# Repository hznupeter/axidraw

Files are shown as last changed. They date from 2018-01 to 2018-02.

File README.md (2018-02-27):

# axidraw 画图机器人
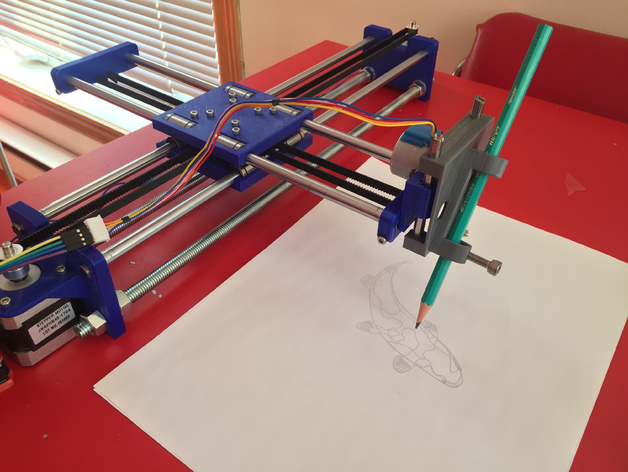
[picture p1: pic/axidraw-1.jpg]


## 3D打印件
打印3d_file 目录下的全部模型，其中x_motor_mount.stl需要打印2份。
模型文件来源https://www.thingiverse.com/thing:1514145

## 硬件
- arduino UNO 1块
- CNC shield v3雕刻机扩展板 1片
- A4988驱动芯片(带散热片) 3片
- 12V 3A监控电源 1个
- 28BYJ-48 5V 步进电机 1个
- 42步进电机 2个
- 短接帽 10个
- M3 8mm 螺丝 2个
- M3 20mm 螺丝10个
- M3 30mm 螺丝8个
- M3螺帽 22个
- M10螺帽 8个
- 直线光轴8mm*400mm 2根
- 直线光轴8mm*300mm 2根
- 直线光轴6mm*100mm 2根
- LM6UU直线轴承 2个
- LM8UU直线轴承 8个
- 2GT-16齿同步轮 内孔5mm 含顶丝 2个
- 16齿同步轮 被动轮 内孔3mm 1个
- 16齿 无齿轮 被动轮 内孔3mm 4个
- 2GT同步带 带宽6mm 2米

## 软件

- [Arduino IDE](https://www.arduino.cc/en/Main/Software)

给arduino UNO烧写固件。

- [grbl库](https://github.com/grbl/grbl)

用于给arduino UNO烧写该库。

- [Inkscape](https://inkscape.org/en/)

一个跨平台的开源软件，利用它的扩展功能可以生成G-code。

- [CNCjs](https://github.com/cncjs/cncjs/releases/latest)

一款CNC控制软件，支持中文，可以方便地将G-code传入到arduino UNO并执行程序。当然也可以使用其他符合grbl规范的软件，如[bCNC](https://github.com/vlachoudis/bCNC),[EleksCAM](http://forum.eleksmaker.com/category/9/elekscam)等。

## 组装

### 电路部分
1. 将CNC扩展板安装在UNO上。
2. 在CNC扩展板的A4988驱动座X、Y、Z中间安装3个短接帽。
3. 将A4988安装到驱动座上。
4. 两个42电机分别连接到X和Y座。
5. 28BYJ-48步进电机连接到Z方向。该步进电机有5根线，可以剪掉红色线，步进电机4跟线与Z轴接口的顺序如下。CNC的电源接口在左侧时，从上到下的顺序依次是：橙色、粉色、蓝色、黄色。
6. CNC扩展板的电源接口接12V3A的监控电源。

### 机械结构
同步带连接采用coreXY结构，具体如下图：

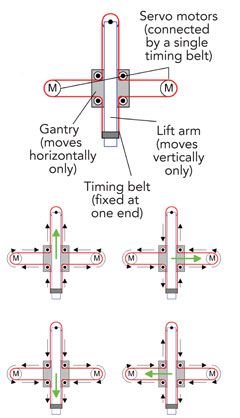
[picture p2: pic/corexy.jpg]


#### 视频参考
http://download.17maker.org/axidraw_1.mp4
#### 图片参考

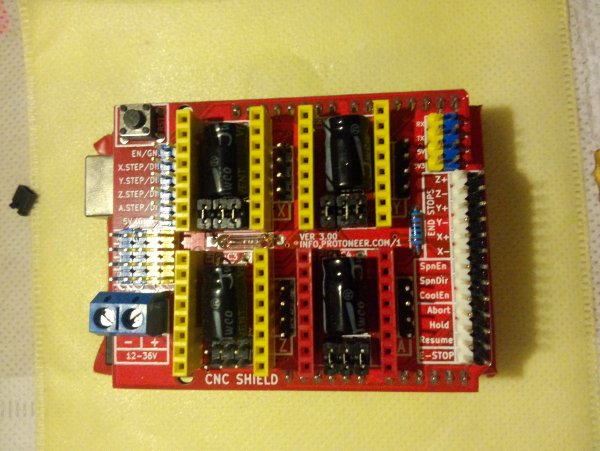
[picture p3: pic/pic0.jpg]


CNC扩展板安装细分短接帽。

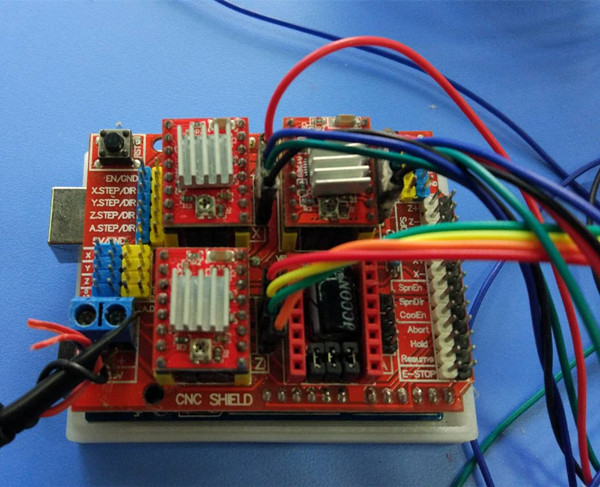
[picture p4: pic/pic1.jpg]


CNC扩展板的接线。

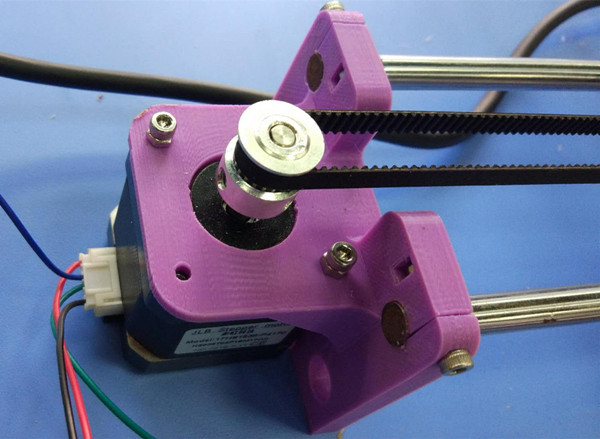
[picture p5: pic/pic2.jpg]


两个电机的安装

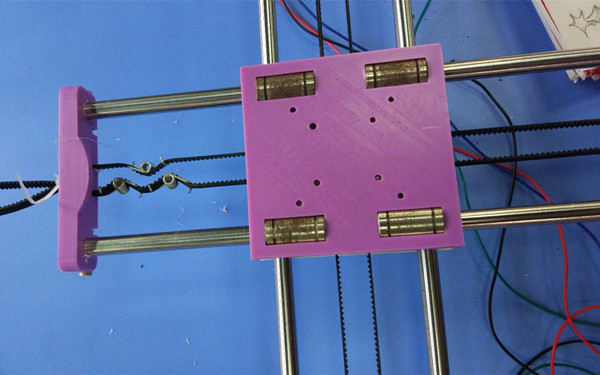
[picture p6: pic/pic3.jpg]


光轴的连接，其中同步带不容易扎紧，可以配几个皮带扭簧使皮带绷紧。

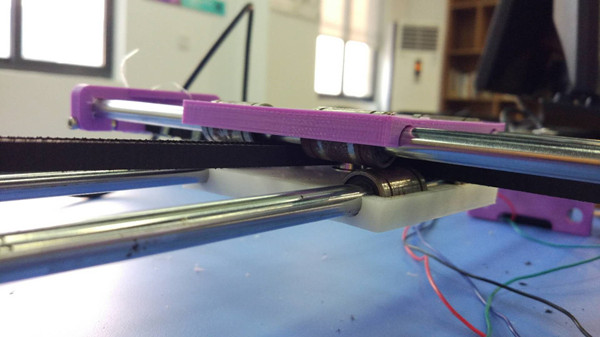
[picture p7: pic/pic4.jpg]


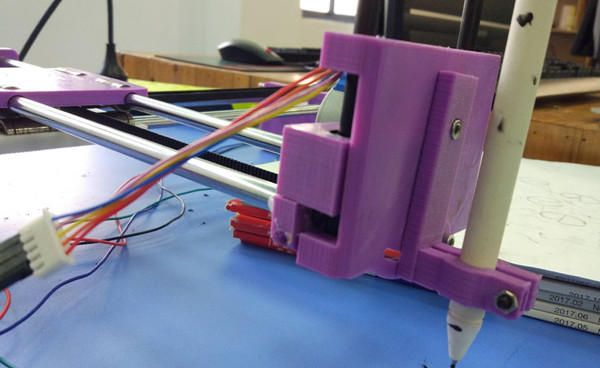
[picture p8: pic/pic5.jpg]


握笔结构，握笔部分的步进电机与CNC扩展板的Z轴相连。

### 固件烧写
- 下载[grbl库](https://github.com/grbl/grbl)并解压
将grbl文件夹放到你的arduino库目录中（库目录一般为C:\Users\Administrator\Documents\Arduino\libraries。具体可以通过文件-首选项-项目文件夹位置 查到）。

- 修改grbl配置文件
由于本机器采用的是coreXY结构，要修改grbl的配置文件。找到config.h
在75行附近位置增加以下两行定义
```C
 #define HOMING_CYCLE_0 (1<<X_AXIS) 
 #define HOMING_CYCLE_1 (1<<Y_AXIS)
```
并注释掉下面的两行定义
``` C
//#define HOMING_CYCLE_0 (1<<Z_AXIS)                // REQUIRED: First move Z to clear workspace.
//#define HOMING_CYCLE_1 ((1<<X_AXIS)|(1<<Y_AXIS))  // OPTIONAL: Then move X,Y at the same time.
```
在154行附近取消下面一行定义的注释，使之生效。
```C
 #define COREXY // Default disabled. Uncomment to enable.
 ```
 修改完成之后，保存config.h文件，打开arduino IDE，找到 文件-示例-grbl-grblupload。打开，并上传到arduino中。

 上传完成后，打开串口监视器，将波特率设为115200，可以看到arduino会传回一些数据，这些是配置信息。

### 软件设置

下载[CNCjs](https://github.com/cncjs/cncjs/releases/latest)软件并安装。
将写字机用USB线连接到电脑上。

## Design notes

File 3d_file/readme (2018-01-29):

模型原地址：
https://www.thingiverse.com/thing:1514145

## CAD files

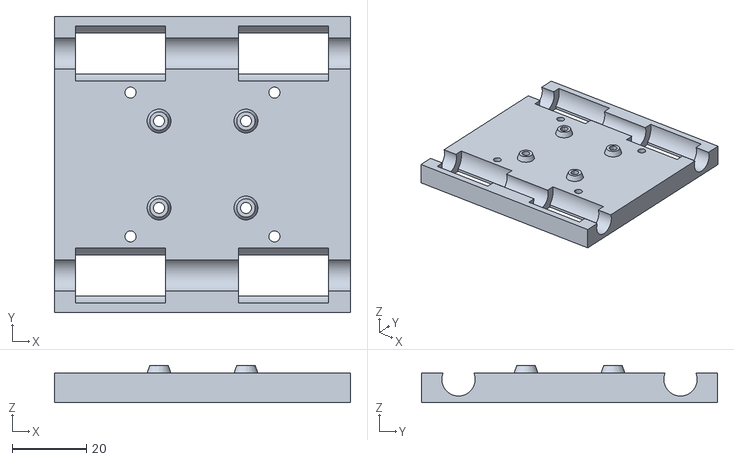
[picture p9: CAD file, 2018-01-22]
3d_file/base_top.stl
80.0 x 80.0 x 10.0

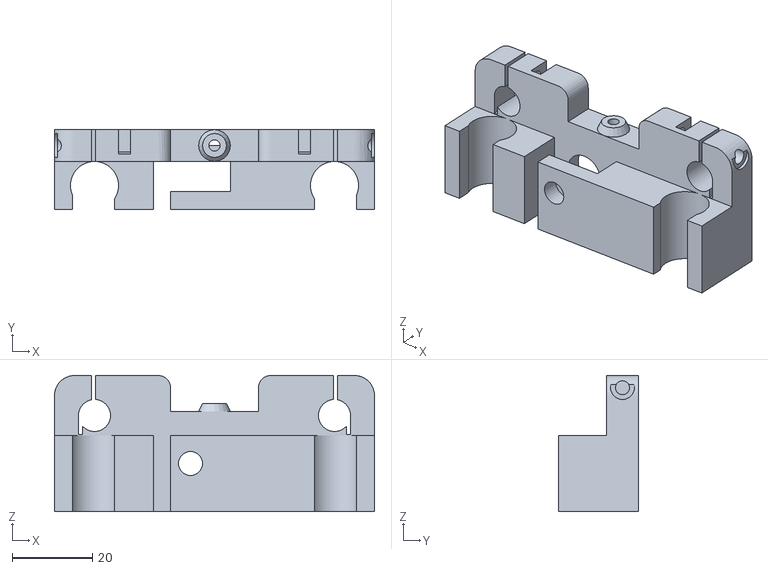
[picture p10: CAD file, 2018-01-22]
3d_file/z_stage.stl
80.0 x 20.0 x 34.0

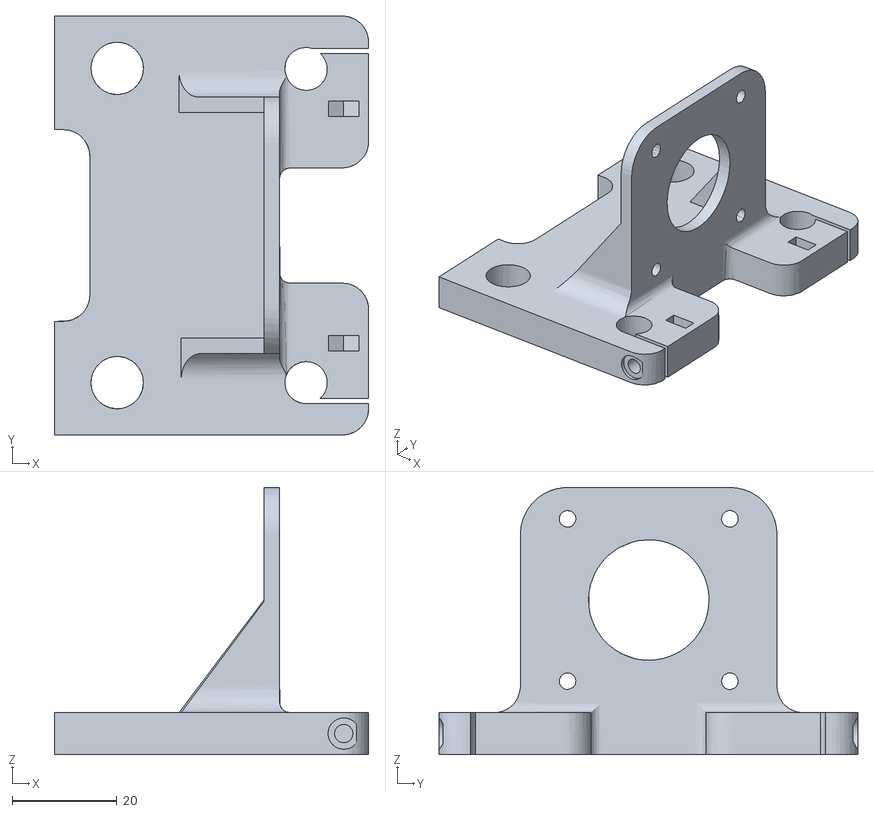
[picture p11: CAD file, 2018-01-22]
3d_file/x_motor_mount.stl
60.0 x 80.0 x 51.0

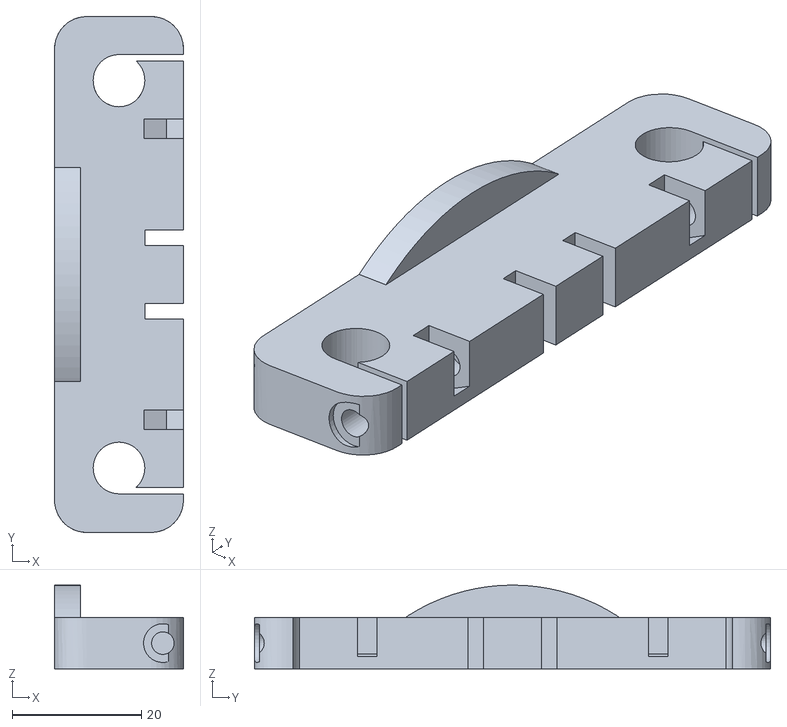
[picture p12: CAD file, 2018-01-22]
3d_file/y_end.stl
20.0 x 80.0 x 13.0

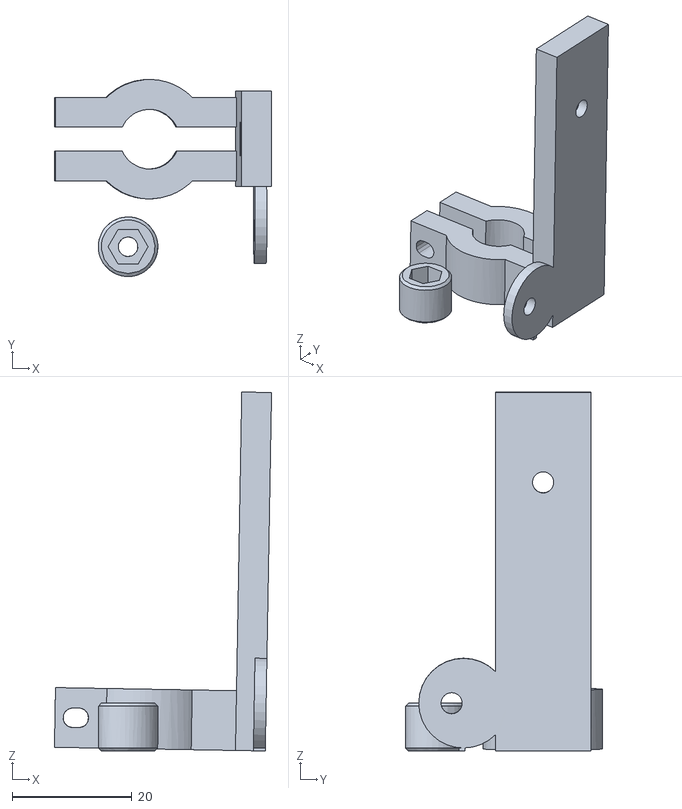
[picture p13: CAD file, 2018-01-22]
3d_file/z_pen_holder.stl
36.3 x 33.0 x 60.1

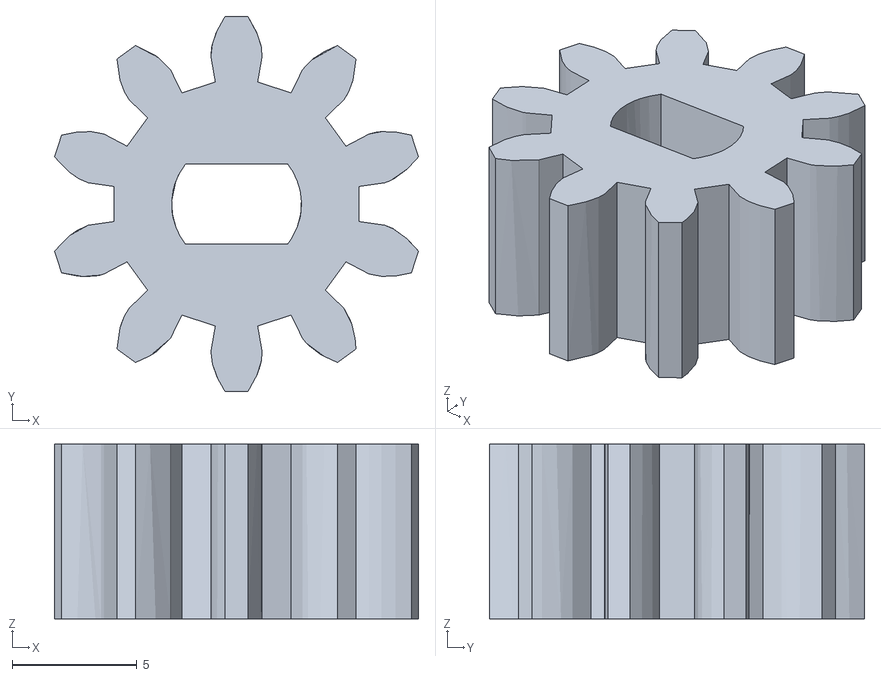
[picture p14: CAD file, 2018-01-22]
3d_file/z_gear.stl
14.6 x 15.0 x 7.00

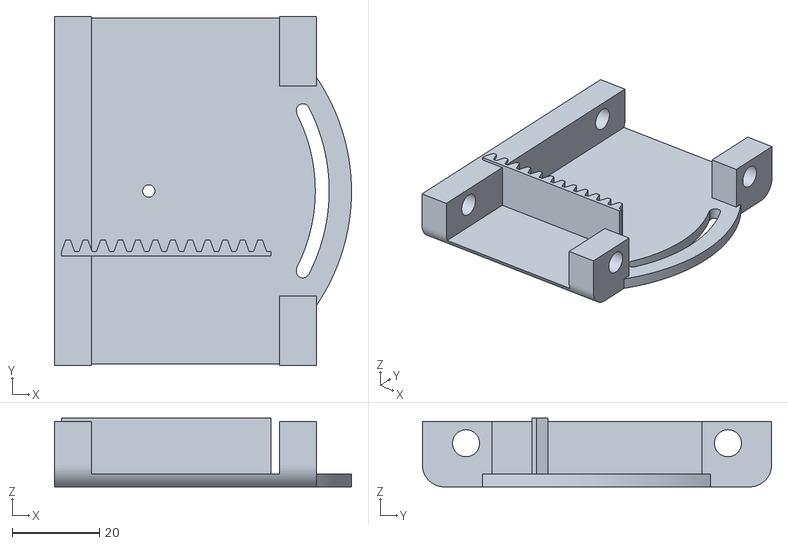
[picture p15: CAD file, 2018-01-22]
3d_file/z_stage_face.stl
68.0 x 80.0 x 15.8

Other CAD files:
3d_file/base_bottom.stl

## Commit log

2018-01-22 add 3D stl
    add 3D stl
    [base_bottom.stl, base_top.stl, brackets.stl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]
2018-01-29 3d地址
2018-01-31 替换图片
2018-01-31 增加图片
2018-01-31 引入图片
2018-01-31 修改图片
2018-01-31 删除视频
2018-01-31 增加 视频连接
2018-02-01 增加图片说明
